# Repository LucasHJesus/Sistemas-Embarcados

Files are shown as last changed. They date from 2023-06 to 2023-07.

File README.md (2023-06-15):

# PAINEL SOLAR SEGUIDOR DE SOL
# (SUN TRACKING SOLAR PANEL)
## Projeto final da matéria de sistemas embarcados

Lucas Humberto Jesus de Lima - 12011ECP011

Bruno Pavan Ciriani da SIlva - 12011ECP012

## Objetivo
 
  O projeto tem como finalidade a construção de um circuito que controla a
rotação(posição relativa) de um painel solar baseado na incidência luminosa, de forma a
maximizar a irradiação na superfície da placa. Tal tarefa é realizada por meio da utilização de
sensores LDR(posicionados nas bordas da placa), cuja medição serve de referência para
rotação em torno do eixo de um servo motor.
Dados como energia gerada em tempo real serão monitorados, exibidos em um display
LCD e armazenados em uma memória externa.

## Principais Requisitos
Para o funcionamento adequado do projeto, existem certos requisitos, como os
seguintes componentes:

* Painel Solar
* Microcontrolador STM32F411CE
* 2 Sensores LDR
* 3 Resistores de 10kΩ
* Servo Motor
* Push Button (NA)
* Placa para apoio do painel solar
* Fios de conexão
* Bateria 9V
* Regulador de Tensão
* Display LCD
* Memória externa e adaptador
* Resistores para medição da energia gerada
  As funções dos principais componentes são:

  Painel Solar : Transforma energia luminosa em energia elétrica.
  
 STM32F411CE: Microcontrolador usado para comparar os sinais enviados e coordenar o
funcionamento dos demais componentes do projeto.

 Sensores LDR: Geram diferentes valores de resistência de acordo com a incidência de luz solar
sobre eles, para serem comparados pelo microcontrolador.
  
 Servo Motor: Rotaciona a placa na direção desejada.

 Push Button: Habilita(ou desabilita) a alimentação do circuito.

 Bateria 9V: Alimentar os componentes do circuito.
  
 Regulador de Tensão: Regula o valor de tensão para o valor usado pelos componentes do
circuito.

  Display: Exibe dados de interesse coletados pelo circuito medidor em tempo real.

  Memória Externa: Armazena dados de interesse coletados pelo circuito medidor.

  Resistores para medição da energia gerada: Divisor de tensão com o intuito de limitar o valor
em 3.3V para que possa ser medido pelo microcontrolador.

## Diagrama de blocos

Diagrama PRJ1

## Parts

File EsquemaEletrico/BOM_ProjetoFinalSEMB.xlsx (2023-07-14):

Item | Qty | Reference(s) | Descrição | Part Number (Mouser) | Preço Unitario($) | Preço total($) | Footprint | Observações | Link
1 | 1 | BT1 | Suporte para bateria de 9V | 12BH611-GR | 1.35 | 1.35 | Footprints:12BH611GR | None | https://br.mouser.com/ProductDetail/Eagle-Plastic-Devices/12BH611-GR?qs=1oCNi33g9sc5AWzrf3Mgtg%3D%3D
2 | 4 | C1, C2, C7,C10 | Capacitor de 1uF | C2220X105K2RACAUTO | 3.19 | 12.76 | Footprints:C2220_FT | None | https://br.mouser.com/ProductDetail/KEMET/C2220X105K2RACAUTO?qs=1mbolxNpo8fmZ3mUaC%2FFGQ%3D%3D
3 | 2 | C3, C12 | Capacitor de 10uF | C2220C106J5RACTU | 4.91 | 9.82 | SamacSys_Parts:capacitor10u | None | https://br.mouser.com/ProductDetail/KEMET/C2220C106J5RACTU?qs=H0q%2F6UITyJhvpLUtE1%252Bnbg%3D%3D
4 | 4 | C4, C5, C6, C8 | Capacitor de 100uF | 12106G107ZAT2A | 1.17 | 4.68 | Footprints:CAPC3225X279N | None | https://br.mouser.com/ProductDetail/KYOCERA-AVX/12106G107ZAT2A?qs=1X9trZCrWl3XQuX3cyRwYQ%3D%3D
5 | 3 | C9, C13,C11 | Capacitor de 0,1uF | C1206C104J1RACAUTO | 0.26 | 0.78 | Footprints:C1206 | None | https://br.mouser.com/ProductDetail/KEMET/C1206C104J1RACAUTO?qs=ds50AKTGxA9j0bB4hqTS6Q%3D%3D
6 | 2 | D1, D2 | Diodo Zener | BZX58550-C6V8-QX | 0.38 | 0.76 | Footprints:diode | None | https://br.mouser.com/ProductDetail/Nexperia/BZX58550-C6V8-QX?qs=7D1LtPJG0i2dEkfKBmD%2FSA%3D%3D
7 | 1 | DisplayOLED1 | Display OLED | SSD1306 | 7.27 | 7.27 | Footprints:128x64OLED | Amazon | https://www.amazon.com/SSD1306/s?k=SSD1306
8 | 1 | IC_OA1 | CI de Amplificadores Operacionais | LM324BIPWR | 0.55 | 0.55 | Footprints:SOP65P640X120-14N | None | https://br.mouser.com/ProductDetail/Texas-Instruments/LM324BIPWR?qs=T%252BzbugeAwjhi0EnhZqTiMg%3D%3D
9 | 2 | LDRsConn1,LDRsConn1 | 2 pinos de conexão | 10129380-902001ALF | 0.15 | 0.3 | Footprints:10129380902001ALF | None | https://br.mouser.com/ProductDetail/Amphenol-FCI/10129380-902001ALF?qs=0lQeLiL1qyaA0bqVZOqelw%3D%3D
10 | 1 | LM317VoltageRegulator1 | Regulador de Tensão | LM317MDT-TR | 0.93 | 0.93 | Package_TO_SOT_SMD:TO-252-2 | None | https://br.mouser.com/ProductDetail/STMicroelectronics/LM317MDT-TR?qs=y7Do%2FCs%252BtTfzGt4t316suA%3D%3D
11 | 1 | LM337VoltageRegulator1 | Regulador de Tensão | LM337KVURG3 | 1.05 | 1.05 | Package_TO_SOT_SMD:TO-252-2 | None | https://br.mouser.com/ProductDetail/Texas-Instruments/LM337KVURG3?qs=iSMark9AYDXYOGB3Dr0rVg%3D%3D
12 | 1 | MIcrocontroler1 | Microcontrolador | STM32F411CEU7 | 7.48 | 7.48 | Package_DFN_QFN:QFN-48-1EP_7x7mm_P0.5mm_EP5.6x5.6mm | None | https://br.mouser.com/ProductDetail/STMicroelectronics/STM32F411CEU7?qs=k5OWtXsTJaprF2FuhgNRlw%3D%3D
13 | 1 | MicroSD1 | Slot de cartão SD | MICRO-SD-CARD | 0.52 | 0.52 | Connector_Card:microSD_HC_Hirose_DM3D-SF | None | https://br.mouser.com/ProductDetail/Olimex-Ltd/MICRO-SD-CARD?qs=Rp5uXu7WBW8fXUZTWj6z0w%3D%3D
14 | 1 | R1 | Resistor de 62R (1%) | ERJ-1TNF62R0U | 1.18 | 1.18 | Footprints:ERJ1T__2512_ | None | https://br.mouser.com/ProductDetail/Panasonic/ERJ-1TNF62R0U?qs=KH2o3k57USgH%2FqWe49afYg%3D%3D
15 | 3 | R2, R3, R8 | Resistores de 1K (1%) | ERJ-1TNF1001U | 0.7 | 2.1 | Footprints:ERJ1T__2512_ | None | https://br.mouser.com/ProductDetail/Panasonic/ERJ-1TNF1001U?qs=KH2o3k57USgAxBX6SLbe%252Bg%3D%3D
16 | 2 | R4, R5 | Resistores de 100k (0.1%) | ERA-8VRB1003V | 1.32 | 2.64 | Footprints:ERA8KEB1004V | None | https://br.mouser.com/ProductDetail/Panasonic/ERA-8VRB1003V?qs=By6Nw2ByBD3GbaEFFbsd4A%3D%3D
17 | 1 | R6 | Resistor de 300R (1%) | ERJ-1TNF3000U | 0.52 | 0.52 | Footprints:ERJ1T__2512_ | None | https://br.mouser.com/ProductDetail/Panasonic/ERJ-1TNF3000U?qs=KH2o3k57USiCiL0iPlOCIw%3D%3D
18 | 1 | R7 | Resistor de 180R (1%) | ERJ-1TNF1800U | 1.18 | 1.18 | Footprints:ERJ1T__2512_ | None | https://br.mouser.com/ProductDetail/Panasonic/ERJ-1TNF1800U?qs=KH2o3k57USh5a4m7W6rgcA%3D%3D
19 | 1 | R9 | Resistor de 10K (0.1%) | ERA-8VRB1002V | 1.32 | 1.32 | Footprints:ERA8KEB1004V | None | https://br.mouser.com/ProductDetail/Panasonic/ERA-8VRB1002V?qs=sGAEpiMZZMtlubZbdhIBINZaoL9yqB51I6UW8FwQKMs%3D
20 | 1 | R10 | Resistor de 240R (1%) | ERJ-1TNF2400U | 1.18 | 1.18 | Footprints:ERJ1T__2512_ | None | https://br.mouser.com/ProductDetail/Panasonic/ERJ-1TNF2400U?qs=KH2o3k57USgZp2v9tl6kYQ%3D%3D
21 | 5 | R11, R12, R13, R14, R15 | Resistores de 4.7k (1%) | ERJ-1TNF4701U | 0.7 | 3.5 | Footprints:ERJ1T__2512_ | None | https://br.mouser.com/ProductDetail/Panasonic/ERJ-1TNF4701U?qs=lpAV6hZbGAvW2ZD2e9jlOA%3D%3D
22 | 1 | R16 | Resistor de 390R (1%) | ERJ-1TNF3900U | 0.7 | 0.7 | Footprints:ERJ1T__2512_ | None | https://br.mouser.com/ProductDetail/Panasonic/ERJ-1TNF3900U?qs=KH2o3k57UShkmhE3TV7Dlg%3D%3D
23 | 6 | R17, R18, R19, R20, R21, R22 | Resistores de 22R (1%) | ERJ-L12KF22MU | 0.75 | 4.5 | Footprints:ERJL12__1812_ | None | https://br.mouser.com/ProductDetail/Panasonic/ERJ-L12KF22MU?qs=bHJq1HQHzUhfotZ%252Bc%252BKipQ%3D%3D
24 | 2 | R23, R24 | Resistores de 2.2K (1%) | ERJ-1TNF2201U | 1.17 | 2.34 | Footprints:ERJ1T__2512_ | None | https://br.mouser.com/ProductDetail/Panasonic/ERJ-1TNF2201U?qs=KH2o3k57USgTJm%252Brf0TwCA%3D%3D
25 | 1 | ServoConn1 | 3 pinos de conexão | 1012938090301BLF | 0.12 | 0.12 | Footprints:10129380903001BLF | None | https://br.mouser.com/ProductDetail/Amphenol-FCI/10129380-903001BLF?qs=0lQeLiL1qyY7ch20dCKSWg%3D%3D
26 | 1 | SolarPanelConn1 | 2 pinos de conexão | 10129380-902001ALF | 0.15 | 0.15 | Footprints:10129380902001ALF | None | https://br.mouser.com/ProductDetail/Amphenol-FCI/10129380-902001ALF?qs=0lQeLiL1qyaA0bqVZOqelw%3D%3D
27 | 2 | SW1, SW2 | Botões para Boot e Reset | PTS526SM08SMTR2L | 0.13 | 0.26 | Footprints:push_button | None | https://br.mouser.com/ProductDetail/CK/PTS526-SM08-SMTR2-LFS?qs=UXgszm6BlbFgRZzlfGAMFg%3D%3D&mgh=1
 |  |  |  | Total | 40.33 | 69.94

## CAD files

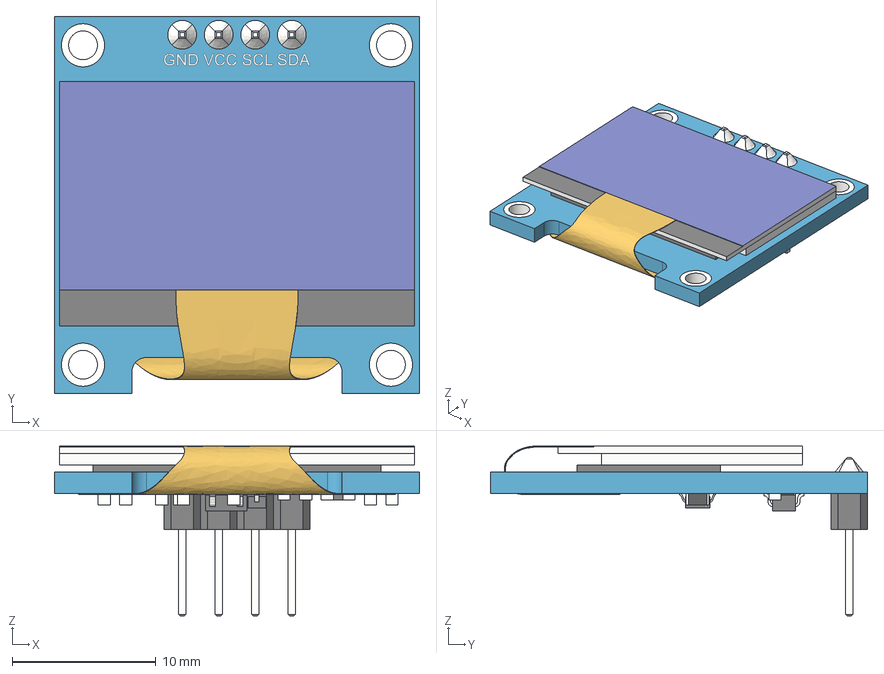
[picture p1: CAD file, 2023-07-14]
EsquemaEletrico/3D models/SSD1306_OLED_Display(128x64).step
25.4 x 26.2 x 11.8 mm
board
screen
pin_header
soldering
smd_capacitor
smd_capacitor (1)
914_smd_resistor
472_smd_resistor x 3
t4_smd_diode
smd_capacitor (2)
smd_capacitor (3)
smd_capacitor (4)
smd_capacitor (5)
smd_capacitor (6)
472_smd_resistor (1)
SOT-23_XC6206 v3
smd_capacitor (7)
flat_cable

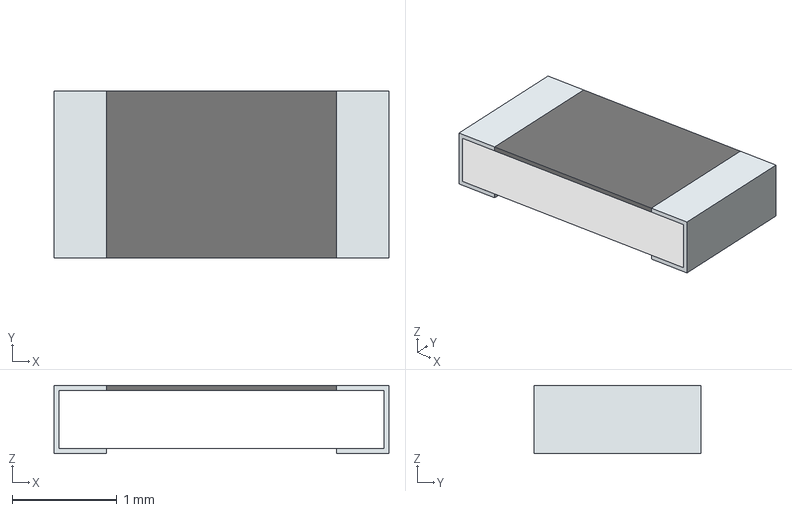
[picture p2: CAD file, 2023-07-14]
EsquemaEletrico/3D models/ERA-8VRB1002V.stp
3.20 x 1.60 x 0.65 mm
solidBody
Terminal
solidLid

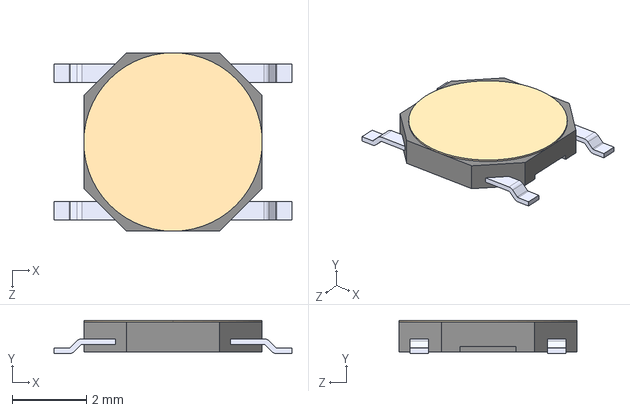
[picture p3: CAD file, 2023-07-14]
EsquemaEletrico/3D models/PTS526_SM08_SMTR2_LFS.stp
6.40 x 0.9 x 4.80 mm

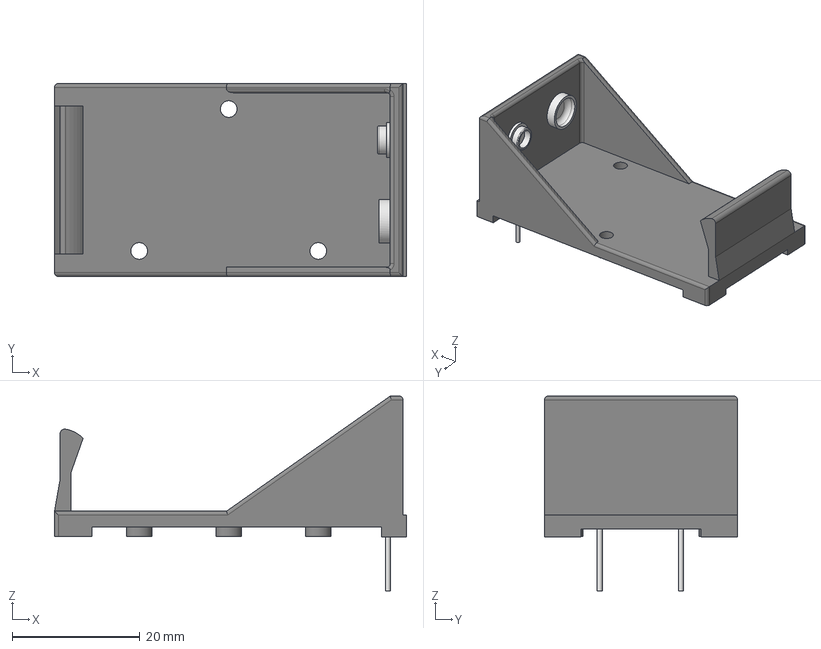
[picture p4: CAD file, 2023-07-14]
EsquemaEletrico/3D models/12BH611-GR.stp
55.0 x 30.2 x 30.5 mm

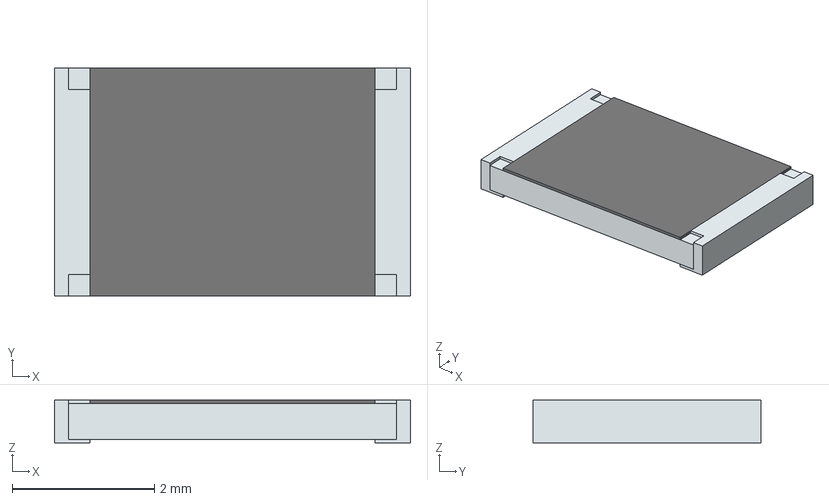
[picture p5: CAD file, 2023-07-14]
EsquemaEletrico/3D models/ERJ-L12KF22MU.stp
5.00 x 3.20 x 0.6 mm
solidBody
Terminal
solidTop

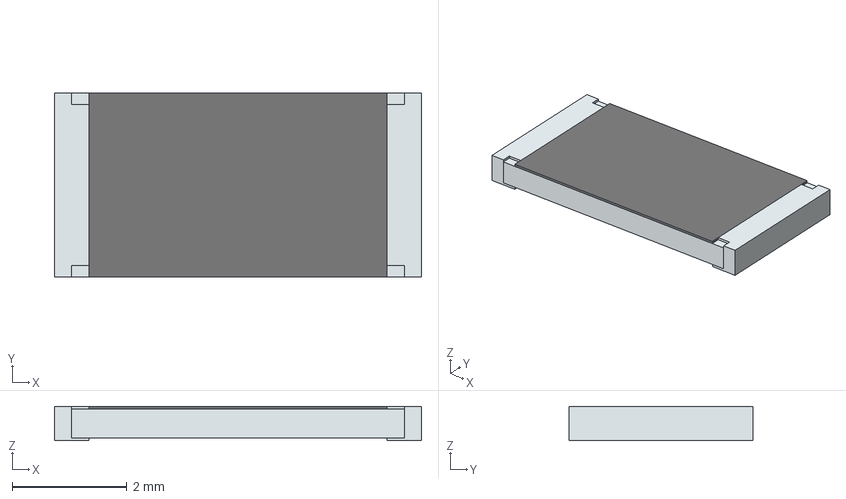
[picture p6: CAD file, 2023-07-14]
EsquemaEletrico/3D models/ERJ-1TNF62R0U.stp
6.40 x 3.20 x 0.6 mm
solidBody
Terminal
solidTop

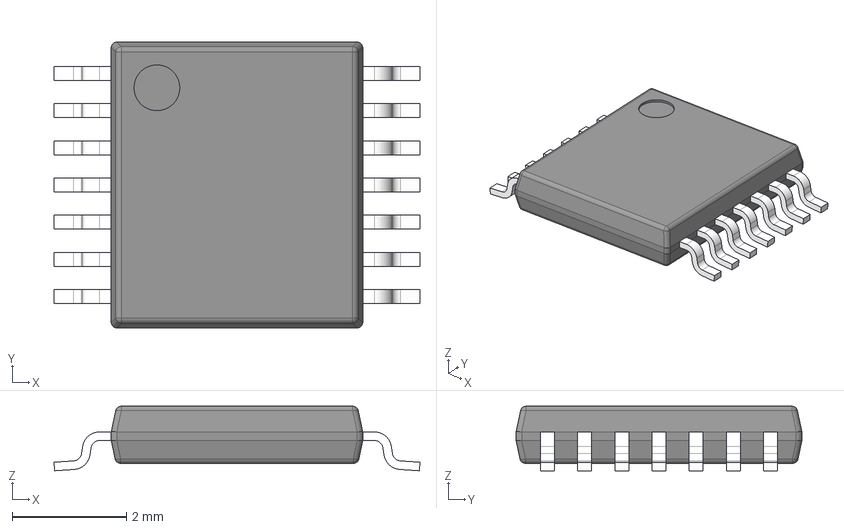
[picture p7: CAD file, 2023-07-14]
EsquemaEletrico/3D models/LM324BIPWR.stp
6.40 x 5.00 x 1.13 mm
BODY-TSSOP
LEAD-TSSOP x 14
PIN1

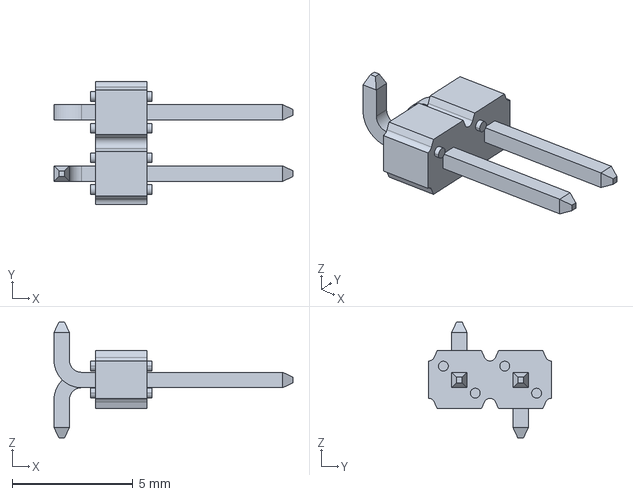
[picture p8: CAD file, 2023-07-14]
EsquemaEletrico/3D models/10129380-902001ALF.stp
9.90 x 5.08 x 4.79 mm

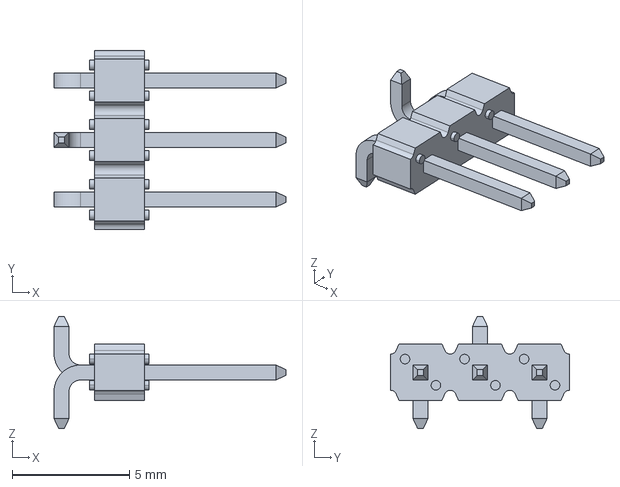
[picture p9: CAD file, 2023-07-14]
EsquemaEletrico/3D models/10129380-903001BLF.stp
9.90 x 7.62 x 4.79 mm

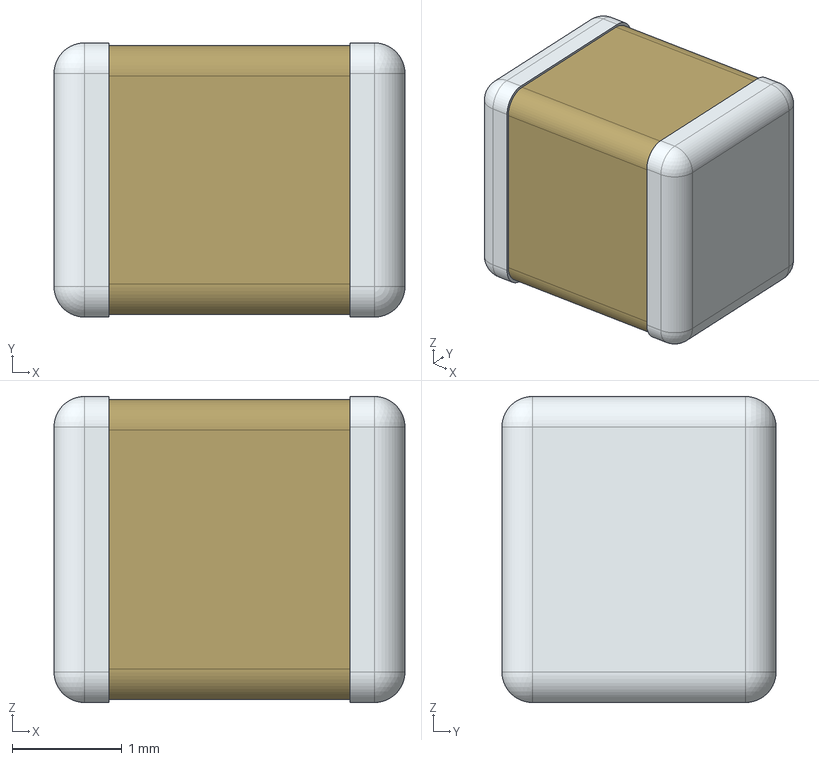
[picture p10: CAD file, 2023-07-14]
EsquemaEletrico/3D models/12106G107ZAT2A.stp
3.20 x 2.50 x 2.79 mm

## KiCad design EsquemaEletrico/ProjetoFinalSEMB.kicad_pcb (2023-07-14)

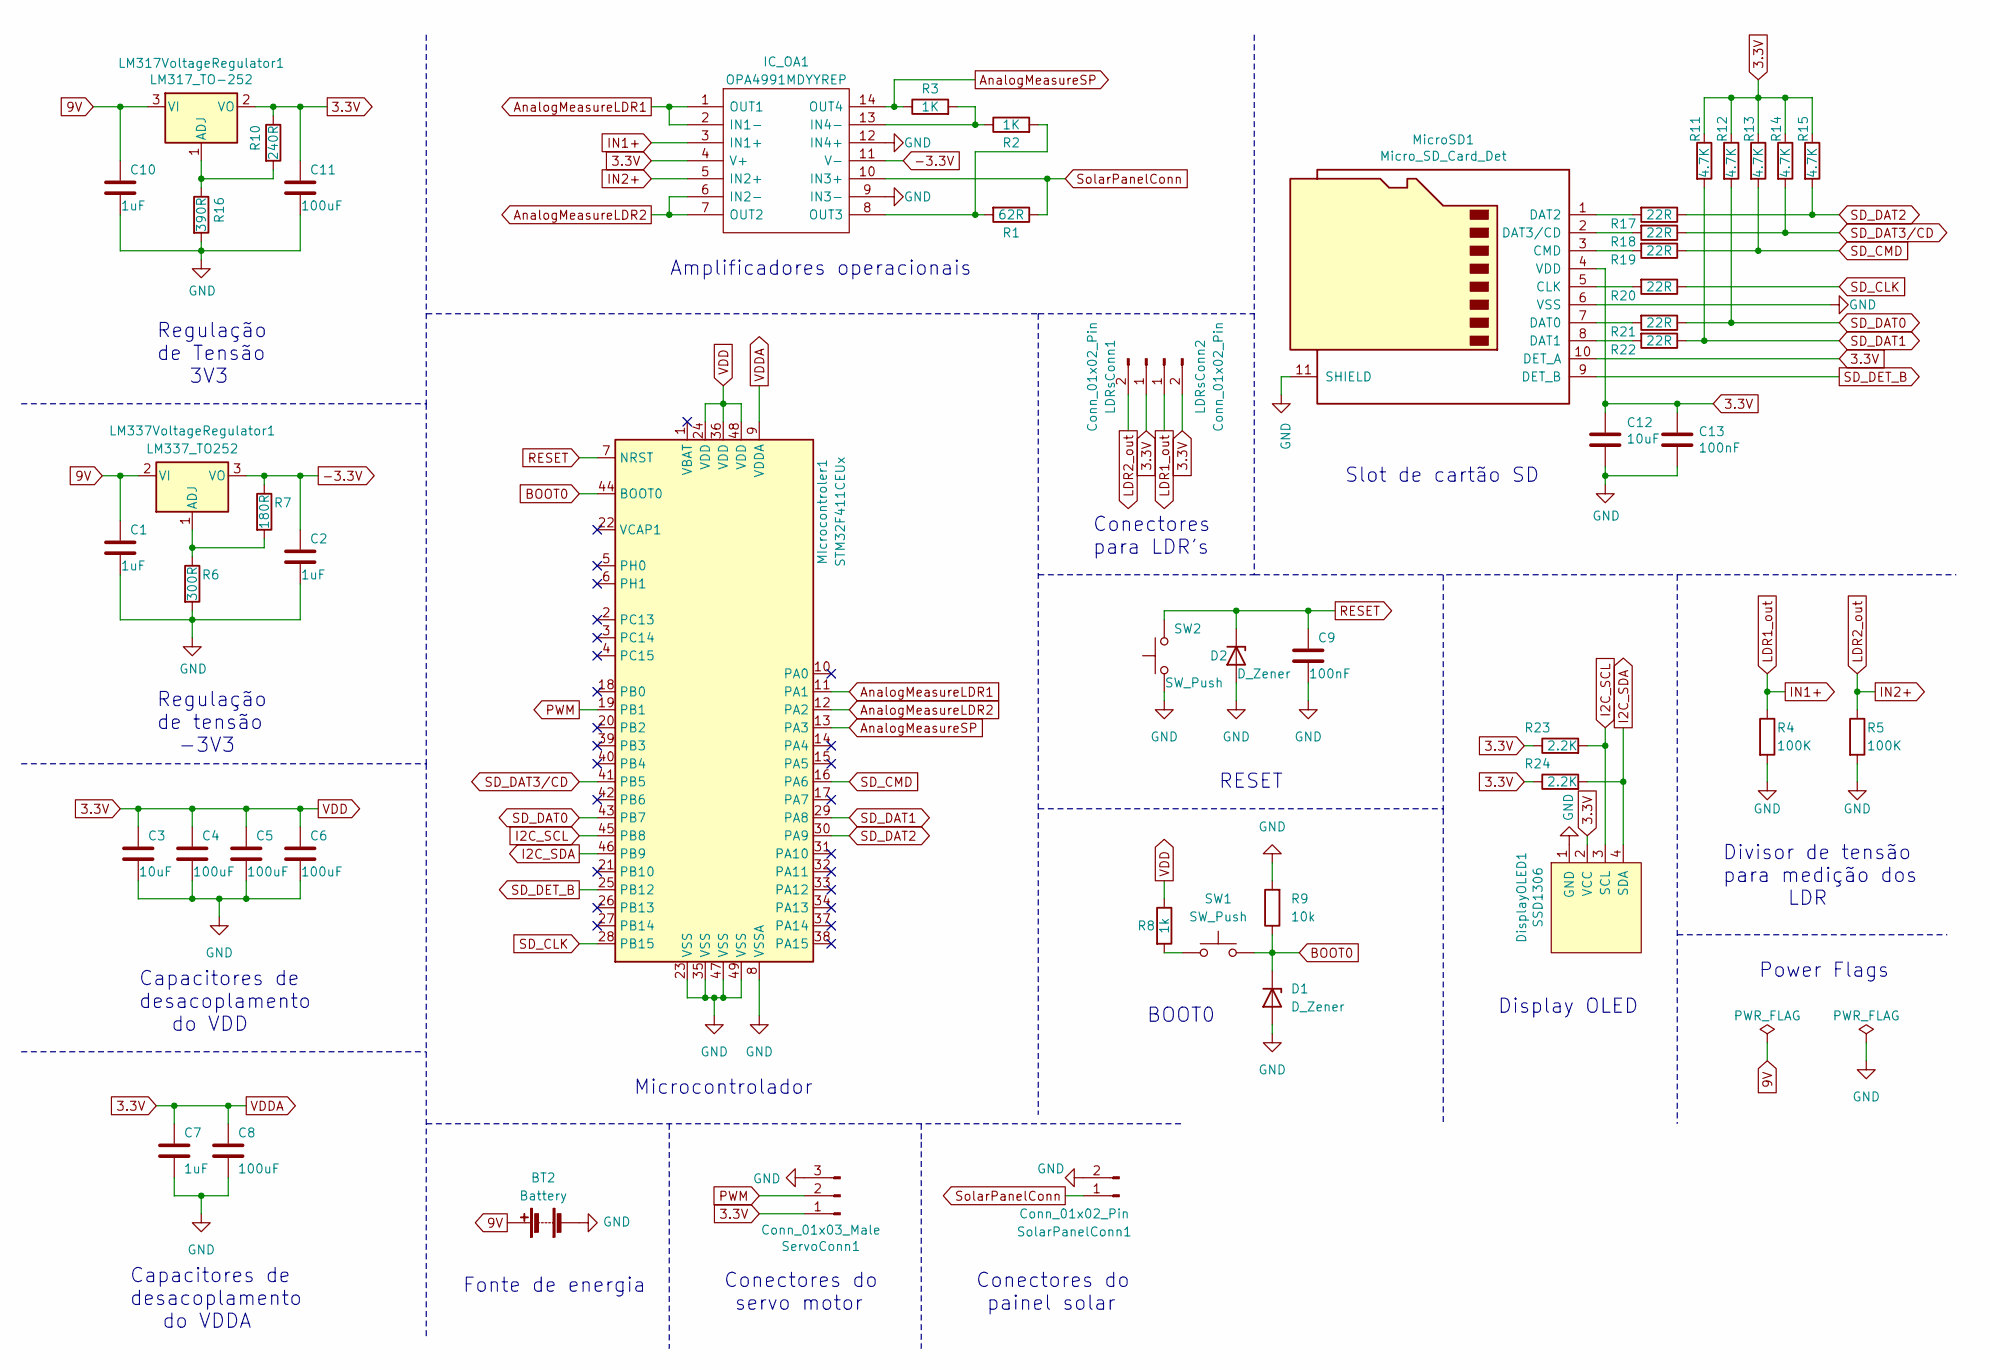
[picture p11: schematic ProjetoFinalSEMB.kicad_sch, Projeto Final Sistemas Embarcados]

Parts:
BT2: Battery; 12BH611GR
C1, C2, C7, C10: 1uF; C2220_FT
C3, C12: 10uF; capacitor10u
C4, C5, C6, C8: 100uF; CAPC3225X279N
C9, C13: 100nF; C1206
C11: 100uF; C1206
D1, D2: D_Zener; diode
DisplayOLED1: SSD1306; 128x64OLED
IC_OA1: OPA4991MDYYREP; SOP65P640X120-14N; Mouser Part Number 595-OPA4991MDYYREP
LDRsConn1, LDRsConn2: Conn_01x02_Pin; 10129380902001ALF
LM317VoltageRegulator1: LM317_TO-252; TO-252-2
LM337VoltageRegulator1: LM337_TO252; TO-252-2
MIcrocontroler1: STM32F411CEUx; QFN-48-1EP_7x7mm_P0.5mm_EP5.6x5.6mm
MicroSD1: Micro_SD_Card_Det; microSD_HC_Hirose_DM3D-SF
R1: 62R; ERJ1T__2512_
R2, R3: 1K; ERJ1T__2512_
R4, R5: 100K; ERA8KEB1004V
R6: 300R; ERJ1T__2512_
R7: 180R; ERJ1T__2512_
R8: 1k; ERJ1T__2512_
R9: 10k; ERA8KEB1004V
R10: 240R; ERJ1T__2512_
R11, R12, R13, R14, R15: 4.7K; ERJ1T__2512_
R16: 390R; ERJ1T__2512_
R17, R18, R19, R20, R21, R22: 22R; ERJL12__1812_
R23, R24: 2.2K; ERJ1T__2512_
SW1, SW2: SW_Push; push_button
ServoConn1: Conn_01x03_Male; 10129380903001BLF
SolarPanelConn1: Conn_01x02_Pin; 10129380902001ALF

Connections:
3.3V: C3.1, C4.1, C5.1, C6.1, C7.1, C8.1, C11.1, C12.1, C13.1, DisplayOLED1.2 (VCC), IC_OA1.4 (V+), LDRsConn1.1, LDRsConn2.2, LM317VoltageRegulator1.2 (VO), MIcrocontroler1.9 (VDDA), MIcrocontroler1.24 (VDD), MIcrocontroler1.36 (VDD), MIcrocontroler1.48 (VDD), MicroSD1.4 (VDD), MicroSD1.10 (DET_A), R8.1, R10.1, R11.1, R12.1, R13.1, R14.1, R15.1, R23.1, R24.1, ServoConn1.1
9V: BT2.1 (+), C1.1, C10.1, LM317VoltageRegulator1.3 (VI), LM337VoltageRegulator1.2 (VI)
-3.3V: C2.1, IC_OA1.11 (V-), LM337VoltageRegulator1.3 (VO), R7.1
AnalogMeasureLDR1: IC_OA1.1 (OUT1), IC_OA1.2 (IN1-), MIcrocontroler1.11 (PA1)
AnalogMeasureLDR2: IC_OA1.6 (IN2-), IC_OA1.7 (OUT2), MIcrocontroler1.12 (PA2)
AnalogMeasureSP: IC_OA1.14 (OUT4), MIcrocontroler1.13 (PA3), R3.1
BOOT0: D1.1 (K), MIcrocontroler1.44 (BOOT0), R9.1, SW1.2
GND: BT2.2 (-), C1.2, C2.2, C3.2, C4.2, C5.2, C6.2, C7.2, C8.2, C9.2, C10.2, C11.2, C12.2, C13.2, D1.2 (A), D2.2 (A), DisplayOLED1.1 (GND), IC_OA1.9 (IN3-), IC_OA1.12 (IN4+), MIcrocontroler1.8 (VSSA), MIcrocontroler1.23 (VSS), MIcrocontroler1.35 (VSS), MIcrocontroler1.47 (VSS), MIcrocontroler1.49 (VSS), MicroSD1.6 (VSS), MicroSD1.11 (SHIELD), R4.2, R5.2, R6.2, R9.2, R16.2, SW2.1, ServoConn1.3, SolarPanelConn1.2
I2C_SCL: DisplayOLED1.3 (SCL), MIcrocontroler1.45 (PB8), R23.2
I2C_SDA: DisplayOLED1.4 (SDA), MIcrocontroler1.46 (PB9), R24.2
IN1+: IC_OA1.3 (IN1+), LDRsConn2.1, R4.1
IN2+: IC_OA1.5 (IN2+), LDRsConn1.2, R5.1
unnamed: IC_OA1.13 (IN4-), R2.1, R3.2
unnamed: IC_OA1.8 (OUT3), R1.2, R2.2
unnamed: LM317VoltageRegulator1.1 (ADJ), R10.2, R16.1
unnamed: LM337VoltageRegulator1.1 (ADJ), R6.1, R7.2
unnamed: MicroSD1.5 (CLK), R20.2
unnamed: MicroSD1.3 (CMD), R19.2
unnamed: MicroSD1.7 (DAT0), R21.2
unnamed: MicroSD1.8 (DAT1), R22.2
unnamed: MicroSD1.1 (DAT2), R17.2
unnamed: MicroSD1.2 (DAT3/CD), R18.2
unnamed: R8.2, SW1.1
PWM: MIcrocontroler1.19 (PB1), ServoConn1.2
RESET: C9.1, D2.1 (K), MIcrocontroler1.7 (NRST), SW2.2
SD_CLK: MIcrocontroler1.28 (PB15), R20.1
SD_CMD: MIcrocontroler1.16 (PA6), R13.2, R19.1
SD_DAT0: MIcrocontroler1.43 (PB7), R12.2, R21.1
SD_DAT1: MIcrocontroler1.29 (PA8), R11.2, R22.1
SD_DAT2: MIcrocontroler1.30 (PA9), R15.2, R17.1
SD_DAT3/CD: MIcrocontroler1.41 (PB5), R14.2, R18.1
SD_DET_B: MIcrocontroler1.25 (PB12), MicroSD1.9 (DET_B)
SolarPanelConn: IC_OA1.10 (IN3+), R1.1, SolarPanelConn1.1

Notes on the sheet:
Conectores para LDR's
Microcontrolador
Conectores do painel solar
Fonte de energia
Slot de cartão SD
Display OLED
Power Flags
BOOT0
Capacitores de desacoplamento do VDDA
Regulação de Tensão 3V3
Conectores do servo motor
Capacitores de desacoplamento do VDD
Regulação de tensão -3V3
Divisor de tensão para medição dos LDR
RESET
Amplificadores operacionais

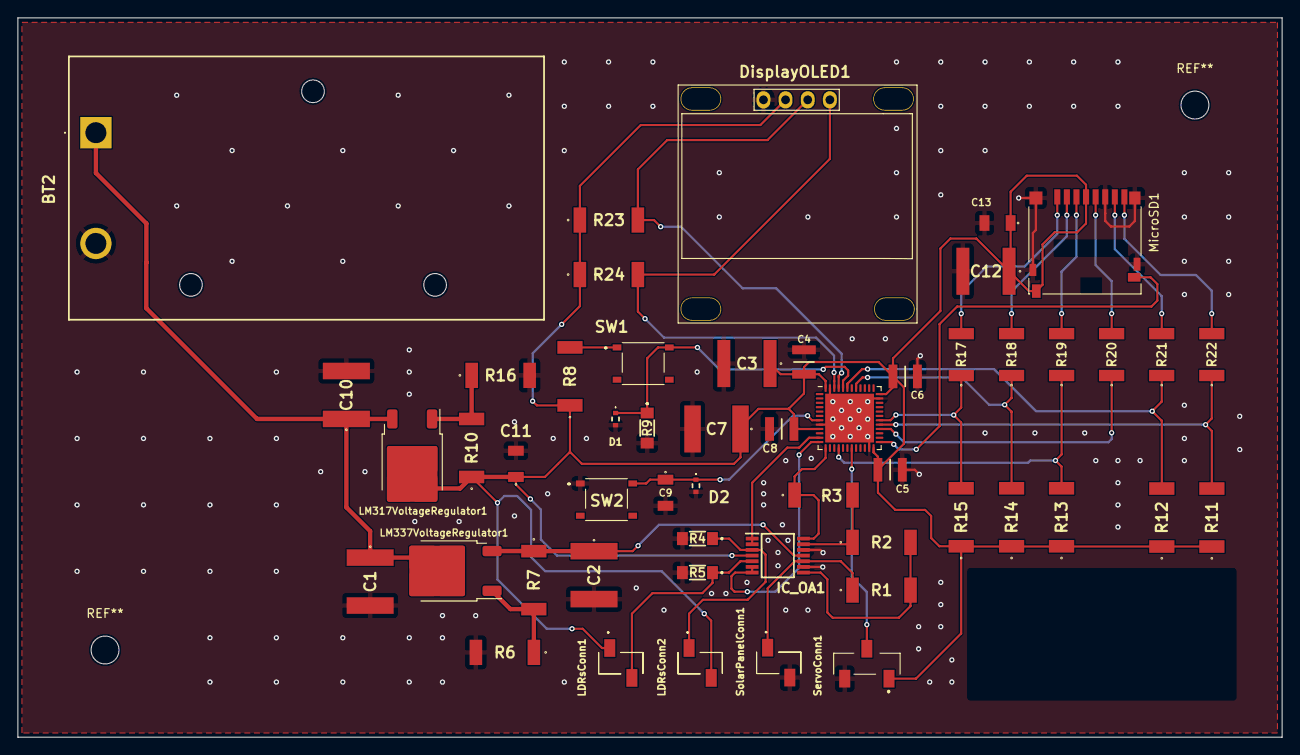
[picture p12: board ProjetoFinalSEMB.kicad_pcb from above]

Board: 2 copper layers, 145.0 x 82.5 mm, 52 parts (0 on the bottom side), 33 nets.

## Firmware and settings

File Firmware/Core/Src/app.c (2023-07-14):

/*
 * app.c
 *
 *  Created on: 23 de jun de 2023
 *      Author: lucas
 */



#include "app.h"
/* returns the the magnitude of value1 with respect to value2 with a
 * differential, so that the servo doesn't move without necessity*/
compare compareValue(int32_t value1,int32_t value2)
{
	if ((value1-TOLERANCE)>value2) return GT;	//if value1 is grater than value2

	if ((value2-TOLERANCE)>value1) return LT;	//if value1 is grater than value2

	return EQ;									//if they are equal


}
/*calculates the discrete integral of the vector spValue
 * uses a Riemann sum with a trapeze as base for the sum*/
float calculateEnergy(float spValue[MAX_COUNT])
{
	int32_t i;
	float sum = 0.0;
	//goes through the spValue vector, except the last value, to avoid accessing unauthorized memory
	for (i = 0; i<(MAX_COUNT-2);i++)
	{
		//sums old value of sum with the current value os the trapeze
		sum += (( spValue[i] + spValue[i+1])*DT ) /TOTAL_TIME;
	}
	return sum;
}

float convertToAmpere(int32_t spValue)
{
	return (MAX_CURRENT/MAX_ADC)*spValue;

}

void setup(void)
{
	hw_displayInit();
	hw_sdInit();
}

void loop(void)
{
	static int32_t temp, index = 0;
	static float spValue[MAX_COUNT];
	float energy;
	//collects data from ldrs
	int32_t ldr1Value = hw_getAnalogValue(LDR1);
	int32_t ldr2Value = hw_getAnalogValue(LDR2);

	//check if its night or not(check light level
	if((ldr1Value<MIN_LIGHT)&&(ldr2Value<MIN_LIGHT))
	{
		hw_servoMoveToZero();
	}
	//compare data collected
	compare comparison = compareValue(ldr1Value,ldr2Value);

	//move servo accordingly
	hw_moveServo(comparison);

	//collect data from solar panel
	temp = hw_getAnalogValue(SOLARPANEL);
	spValue[index] = OUTPUT_TENSION * convertToAmpere(temp);
	index+=1;

	/*after 30min(60 data collection cycles) calculated
	energy generated and store it in sd-card*/
	if (index == MAX_COUNT)
	{
		//calculate energy
		energy = calculateEnergy(spValue);
		//store in sd-card
		hw_sdStore(energy);
		//show on display
		hw_displayShow(energy);

		index = 0;
	}


	//sets the processor in wait for interruption mode
	hw_sleep();
}

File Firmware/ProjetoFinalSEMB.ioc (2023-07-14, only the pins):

Mcu.UserName=STM32F411CEUx
PA1.GPIO_Label=LRD1_MEASURE
PA1.Signal=SharedAnalog_PA1
PA13.Signal=SYS_JTMS-SWDIO
PA14.Signal=SYS_JTCK-SWCLK
PA2.GPIO_Label=LRD2_MEASURE
PA2.Signal=SharedAnalog_PA2
PA3.GPIO_Label=SP_MEASURE
PA3.Signal=SharedAnalog_PA3
PA6.Signal=SDIO_CMD
PA8.Signal=SDIO_D1
PA9.Signal=SDIO_D2
PB1.Signal=S_TIM3_CH4
PB12.Signal=GPIO_Input
PB15.Signal=SDIO_CK
PB5.Signal=SDIO_D3
PB7.Signal=SDIO_D0
PB8.Signal=I2C1_SCL
PB9.Signal=I2C1_SDA

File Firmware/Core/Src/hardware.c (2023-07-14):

/*
 * hardware.c
 *
 *  Created on: 23 de jun de 2023
 *      Author: lucas
 */
#include "hardware.h"

extern TIM_HandleTypeDef htim3;//PWM timer
extern TIM_HandleTypeDef htim1;//wake up timer
extern ADC_HandleTypeDef hadc1;//ADC channel
extern I2C_HandleTypeDef hi2c1;//I2C instance
extern SD_HandleTypeDef hsd;//sd card instance

//Activates the timer to wake up the processor and enters wait for interuption mode
void hw_sleep(void)
{
	HAL_TIM_Base_Start_IT(&htim1);
	__WFI();
}

/*configures wich one of the three channels the ADC will convert
Recives a int32_t that specifies the channel*/
void hw_adcChannelConfig(int32_t channel)
{
	//create a ADC_ChannelConfTypeDef object and fills it
	ADC_ChannelConfTypeDef sConfig = {0};
	sConfig.Channel = channel;
	sConfig.Rank = 1;
	sConfig.SamplingTime = ADC_SAMPLETIME_3CYCLES;

	//configures the channel
	if (HAL_ADC_ConfigChannel(&hadc1, &sConfig) != HAL_OK)
	{
		Error_Handler();
	}
}

/* recieves an ADC channel to read
 * returns a int32_t between 0 and 4095 informing the ADC read value */
int32_t hw_getAnalogValue(analog entry)
{
	//variables to set the channel and store the read value
	int32_t channels[] ={ADC_CHANNEL_1,ADC_CHANNEL_2,ADC_CHANNEL_3};
	int32_t adcValue;

	//channel configuration
	hw_adcChannelConfig(channels[entry]);

	//ADC read by polling
	HAL_ADC_PollForConversion(&hadc1, 1000);
	adcValue = HAL_ADC_GetValue(&hadc1);
	HAL_ADC_Stop(&hadc1);

	return adcValue;
}

/*Uses the PWM to rotate the servo, recives the direction in wich to rotate*/
void hw_rotate(int32_t side)
{
	//get CCR and ARR
	int32_t CCR = __HAL_TIM_GET_COMPARE(&htim3,TIM_CHANNEL_4);
	int32_t ARR = __HAL_TIM_GET_AUTORELOAD(&htim3);

	//calculates duty new cicle and corresponding ARR value(uses the old to calculate)
	float newDutyCicle = (CCR/ARR) + side * DUTY_CICLE_STEP ;
	int32_t newCCR = (int32_t) ARR * newDutyCicle;

	//sets CCR to newCCR
	__HAL_TIM_SET_COMPARE(&htim3,TIM_CHANNEL_4,newCCR);
}

/*Moves the servo in a direction dependent on the side*/
void hw_moveServo(int32_t side)
{
	//in case side is none
	if (!side) return;
	//moves in LDR1's direction
	if (side == LDR1)
	{
		hw_rotate(UP);
	}
	//moves in LDR2's direction
	else
	{
		hw_rotate(DOWN);
	}
}
/*Moves servo to the start position*/
void hw_servoMoveToZero(void)
{
	//get ARR
	int32_t ARR = __HAL_TIM_GET_AUTORELOAD(&htim3);
	//Caculate CCR
	int32_t newCCR = (int32_t) ARR * MIN_DUTY_CICLE;
	//set CCR
	__HAL_TIM_SET_COMPARE(&htim3,TIM_CHANNEL_4,newCCR);
}
/*Gets the display ready to use*/
void hw_displayInit(void)
{
	//first and third line strings
	char string1[] = "Energia gerada";
	char string2[] = "w/h";

	//start the display
	ssd1306_Init();

	//set cursor to first line and writes first message
	ssd1306_SetCursor(5, 5);
	ssd1306_WriteString(string1, Font_7x10, White);

	//set cursor to third line and writes third message
	ssd1306_SetCursor(5,25);
	ssd1306_WriteString(string2, Font_7x10, White);

	//updates screen
	ssd1306_UpdateScreen();

}

/* shows value on display*/
void hw_displayShow(float energy)
{
	//convert float to char
	char energyChar[16];
	sprintf(energyChar,"%f",energy);

	//set cursor to second line and writes energy production
	ssd1306_SetCursor(5,15);
	ssd1306_WriteString(energyChar,Font_7x10 , White);

	//updates screen
	ssd1306_UpdateScreen();
}

/*gets the sd card ready to use*/
void hw_sdInit(void)
{
	//mounts the sd card
    FATFS fs;
    f_mount(&fs, DEFAUT_PATH, DEFAUT_MOUNT);
}

//writes data to the sd card
void hw_sdStore(float energy)
{
	//in case the sd card isn't connected, doesn't try to write
	if (!HAL_GPIO_ReadPin(GPIOB,GPIO_PIN_12)) return;

	//FATFS variables, used to write to a .txt
	FATFS fs;
	FIL file;
	UINT bw;

	char fileName[] = "out.txt";
	char energyChar[16];

	//data conversion from float to string
	sprintf(energyChar,"%f",energy);

	/*writes to the sd card, mount the card, opens the file,
	writes data, closes the file and unmounts the card*/
	f_mount(&fs, DEFAUT_PATH, DEFAUT_MOUNT);
	f_open(&file, fileName, FA_WRITE | FA_CREATE_ALWAYS);
	f_write(&file, energyChar, SIZE, &bw);
	f_close(&file);
	f_unmount(DEFAUT_PATH);
}

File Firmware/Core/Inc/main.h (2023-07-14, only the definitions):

#define LRD1_MEASURE_Pin GPIO_PIN_1
#define LRD1_MEASURE_GPIO_Port GPIOA
#define LRD2_MEASURE_Pin GPIO_PIN_2
#define LRD2_MEASURE_GPIO_Port GPIOA
#define SP_MEASURE_Pin GPIO_PIN_3
#define SP_MEASURE_GPIO_Port GPIOA

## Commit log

2023-06-15 adição do esquema eletrico e firmware feitos para a primeira entrega
    [BOM_ProjetoFinalSEMB.xlsx, ProjetoFinalSEMB.csv, ProjetoFinalSEMB.kicad_pcb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]
2023-06-15 some fixes
    [ProjetoFinalSEMB.kicad_sch]
2023-07-14 Projeto final completo
    [10129380-902001ALF.stp, 10129380-903001BLF.stp, 12106G107ZAT2A.stp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]

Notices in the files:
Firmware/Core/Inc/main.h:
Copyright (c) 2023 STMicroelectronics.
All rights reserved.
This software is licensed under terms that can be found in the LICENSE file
